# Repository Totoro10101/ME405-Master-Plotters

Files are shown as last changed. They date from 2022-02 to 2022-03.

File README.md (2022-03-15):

# ME405 Master Plotters
### A ME 405 term project that documents a pen plotter design.

The design we're going with is inspired by this YouTube video by DAZ projects: 

[the SIMPLEST cnc PEN PLOTTER | how to build it](https://www.youtube.com/watch?v=zFRRUZdz1HY)

Although we're taking inspriation from this design, we are making some changes that we believe will improve
its performance. The basic layout of this design is a 2.5-D pen plotter that is laid out horizontally on a flat base. The base is
is going to be a rectangular plywood piece with pulleys at each corner. There will be two gearmotors driving the pen plotter placed
at two adjacent corners (see sketch). The two motors will directly drive the two pulleys at the corners of the base, and the two other 
pulleys will be idlers which guide the belt. They will make the belt form one continuous loop in an hourglass shape.
Instead of using string like the video, we will use a GT2 timing belt to increase the traction on the pulley because of the teeth
present on the pulley wheels and the belts, and eliminate slipping. Since the total length of the belt will change slightly as the pen moves,
we will use a stretchy paracord joined with the timing belt to provide some room for movement while keeping tension. To actuate the pen and lift it
off of the paper when moving between drawn lines, we'll use a small servo that activates to lift the pen within its holder. This holder will have
ball rollers on the bottom to allow it to move smoothly over the paper.

A rough bill of materials is shown below. We're keeping the main motors simple and efficient by using the equipment available to us in lab. The GT2 belt and
pulleys will be purchased from Amazon and other components to hold the pen and servo and to mount the motors will be 3D printed by our group.

## Bill of Materials
| Qty. | Part | Source | Est. Cost |
|:----:|:---|:---|:---:|
|  2 | Pittperson Gearmotors | ME405 Tub | - |
|  1 | Nucleo with Shoe | ME405 Tub | - |
|  1 | GT2 Timing Belt | Amazon | $6.99 |
|  1 | GT2 Timing Pulleys | Amazon | $7.99 |
|  4 | Mini Ball Transfer Bearing | Amazon | $10.95  |
|  6 | Skateboard Bearings | Jackson | - |
|  1 | Sunfounder Micro Servo | Charlie | - | 
|  1 | Bungee Cord 1/8" Diameter | Amazon | $5.95 | 
|  1 | Small String | Tori | - |
|  2 | Limit Switches | Amazon | $2 |
|  1 | 3D print fillament | Jackson | - |

## Preliminary System Sketch
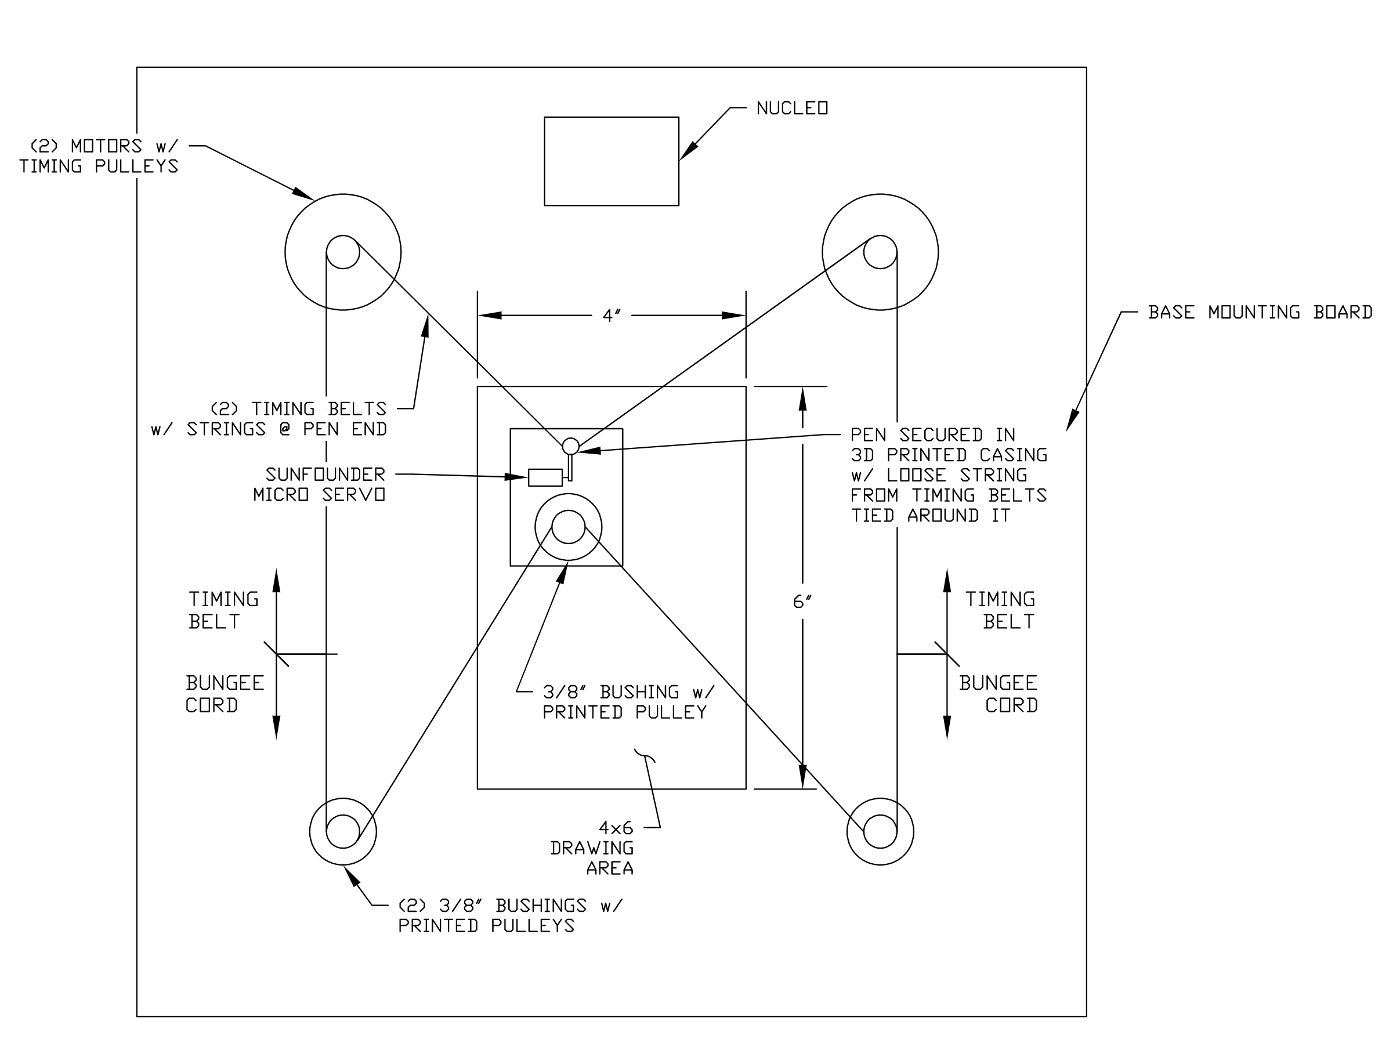
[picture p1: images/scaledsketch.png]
|  |
|:--:|
|**Figure 1: Scaled sketch showing the basic layout of our planned plotter**|

## Hardware Design
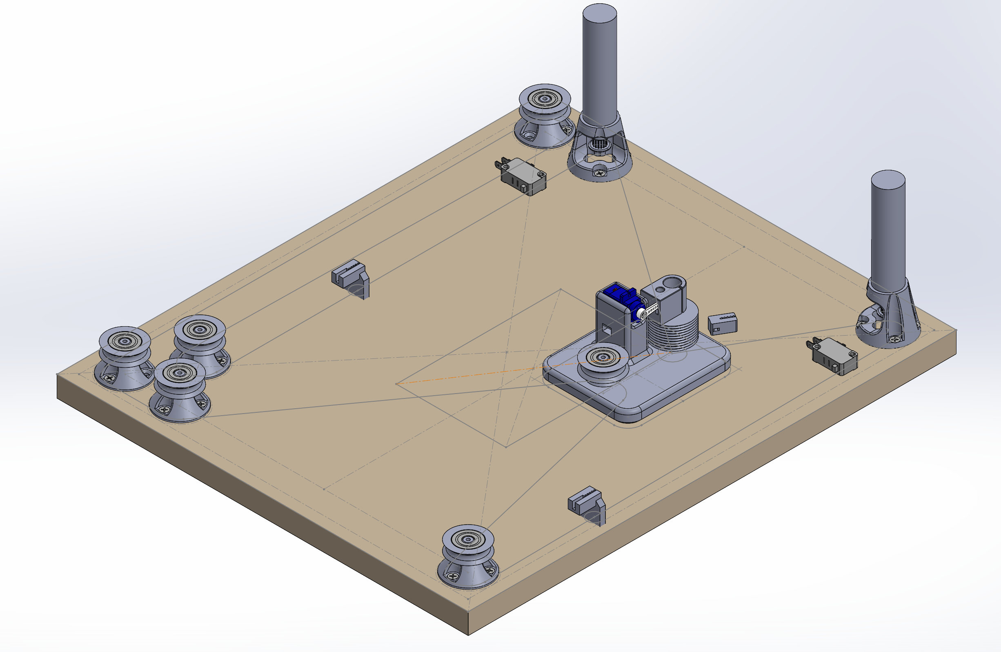
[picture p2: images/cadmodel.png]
|  |
|:--:|
|**Figure 2: CAD Model showing final version of Pen Plotter**|

The hardware we are using is mostly 3D printed from CAD designs created in Solidworks. The main components are the motor mounts, paracord pulleys, 
the pen carriage, and servo mount for actuating the pen. The motor mounts allow for mounting of our gearmotors vertically with the GT2 timing pulleys
housed within the mount and connected to the bungee cord. The pulleys at the adjacent corners that are not driven are using skateboard bearings mounted on top
of similar mounts to ensure the cord is at the same height as the timing belt. One feature that we added since the preliminary sketch phase was a wrap around
pulley for the bungee cord. The extra length of the cord wrapping around this additional pulley ensures we keep proper tension on the timing belt at all locations
in the drawing area, otherwise the bungee could loosen up too much and the belts would slip. The timing belt and cord are connected to the pen carriage at the top
and bottom of the rectangular carriage. There is a pulley on the back to allow the para cord to move smoothly, but the timing belts are attached using string to keep 
the distance constant from the gearmotors to the pen carriage. The pen is attached using a 3D printed holder that contains a cutout to press fit the sharpie into 
the hole. This is then connected to the servo that is mounted on the carriage using the small servo arm and an indentation for the servo to lift up the pen. The pen
carriage itself uses small ball transfer bearings to slide smoothly across the paper while the pen plots.

## Software Design
The software we designed uses a task based approach to update encoder positions and control set points based on a given HPGL file. The first process
to run is the start up process that zeros our encoders and puts the pen carriage in a known home position for us to use as a reference point to calculate 
set points from the HPGL file. The parsed HPGL file gives coordinates in the form of encoder ticks using a coordinate transformation that calculates it 
based on the HPGL and then sets the set point for each motor individually. The controller and encoder constantly update and share the data they collect
to tell whether the pen has reached the proper set point. 

For more detailed explanation on the tasks being performed, refer to our [Github Pages Documentation](https://totoro10101.github.io/ME405-Master-Plotters/)

## Results
The results of our pen plotter were very encouraging. By the end of thep project, we were able to perform relatively complex drawings that included both 
straight lines and curves, pen up and pen down commands, and could be taken from any file drawn in Inkscape so long as there were no memory issues with the
HPGL and the Nucleo. 

We tested the functionality of our pen plotter by providing it with multiple different HPGL files that we believed covered all the important aspects of the 
machine. We needed a file that would move in straight lines as well as curves and also required the lifting of the pen between operations. So long as the 
plotter was able to perform all of these tasks and draw the desired shapes, we believed it would be robust enough of a design to handle any HPGL file. 
The system performed fairly well in these tests once we got the controller set points and kinematics all correct. One minor issue is that the device moves 
more quickly in the direction that the bungee is pulling it in, so it was a little bit less accurate in that direction. Another thing we noticed in testing the 
plotting was that the Inkscape HPGL sometimes included a feature to run over all line commands twice, so it would draw something, and then attempt to go right back over it 
for a darker drawing. This functionality showed us that it wasn't perfectly repeatable due to some steady state error and overshoot in our controller or the bungee
affecting the path too much for repeatability, so the second time a line was plotted, it wasn't perfectly overlapping the original line. This could be fixed with 
some more tuning to controller gains or bungee length, but the variation in repeatability was small enough for our uses. 

## Future Work
Both the hardware and software of the plotter could be improved. One issue previously mentioned was the difference in speed when moving directions due to the
tension in the bungee being uneven for different positions of the pen. This could be mitigated by adding even more length to the bungee run, which makes the force more constant.
There was also some non-negligible friction in the bearings of the idler pulleys. If this were reduced, the difference in effort between each motor could be reduced.
Another way to reduce these effects could be to make the entire system larger, with longer belts, while retaining the same plotting area. The belts were able to stay on
their pulleys without slipping during operation, but this was marginal and they would slip if the pen ended up far outside the drawing area. This could potentially be reduced
with larger drive pulleys, though this would also increase the error from the true position that comes from our calculation of the kinematics of the system. We assume that the
belt extends from the center of the drive motor and its length is proportional to the angle which the pulley has rotated through, but neither of these is strictly true.
With a bigger pulley, we may need to revise this calculation to take into account the radius of the pulleys and the variable amount of belt that wraps around them
as the angle of the belt changes. This does have a unique solution for each point, but requires solving a system of equations since each belt affects the other.

Another improvement to the software would be the ability to draw images with a large number of points. However, we began to run into the limits of the Nucleo's
memory. This issue could be fixed in a few ways. First, it would be good to switch to reading the HPGL file sequentially instead of loading the entire contents into memory.
This alone would be an improvement, but to allow for any reasonable file to be drawn, it may be necessary to queue up points as the plotter is drawing. HPGL is read
sequentially, so it would be possible to integrate the parsing of the file into the multitasking loop, which would mean that the limitation would be the size of the flash
on the Nucleo. This is likely large enough for any reasonable plots, but if not external storage such as an SD card could be used, or HPGL could be sent over serial.

## Additional Links
[Github Pages Documentation](https://totoro10101.github.io/ME405-Master-Plotters/)

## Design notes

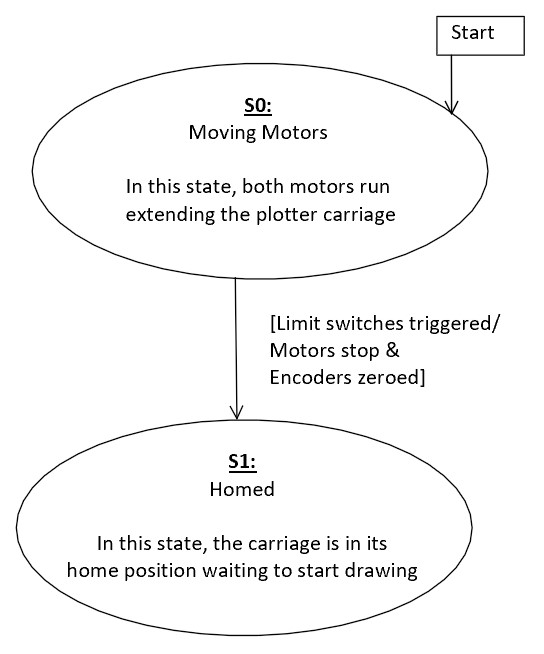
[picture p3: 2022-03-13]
docs/task_startup_FSM.jpg

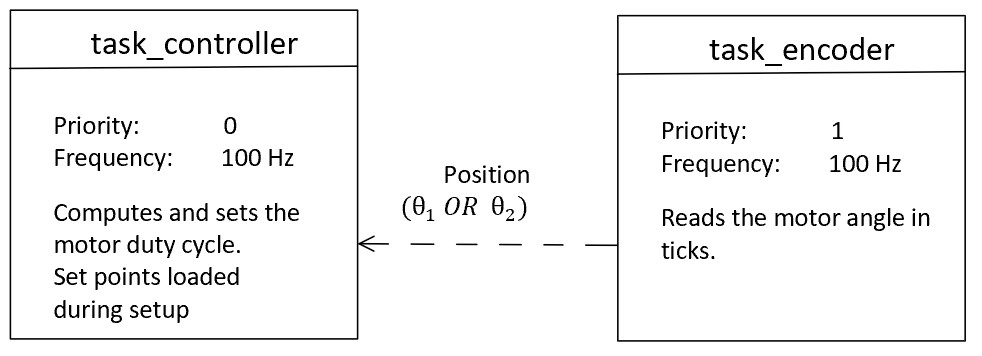
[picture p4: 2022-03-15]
docs/task_diagram.jpg

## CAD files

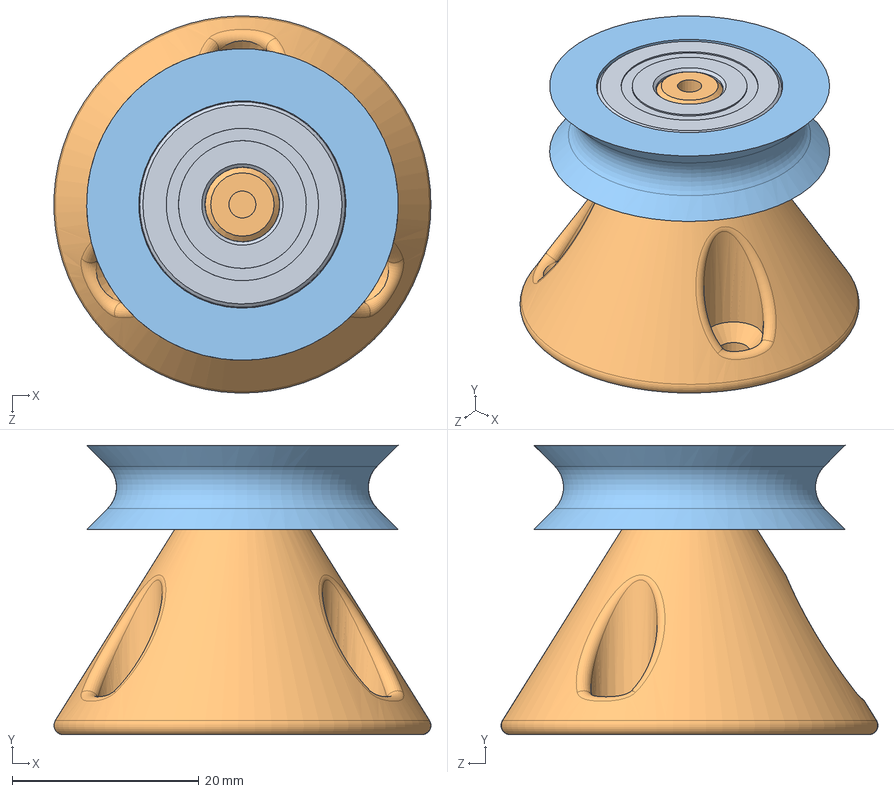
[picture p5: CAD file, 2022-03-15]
cad/solidworks/idler mounted.SLDASM
40.4 x 31.0 x 40.4 mm
6661K12_Ball Bearing
idler mount
idler pulley

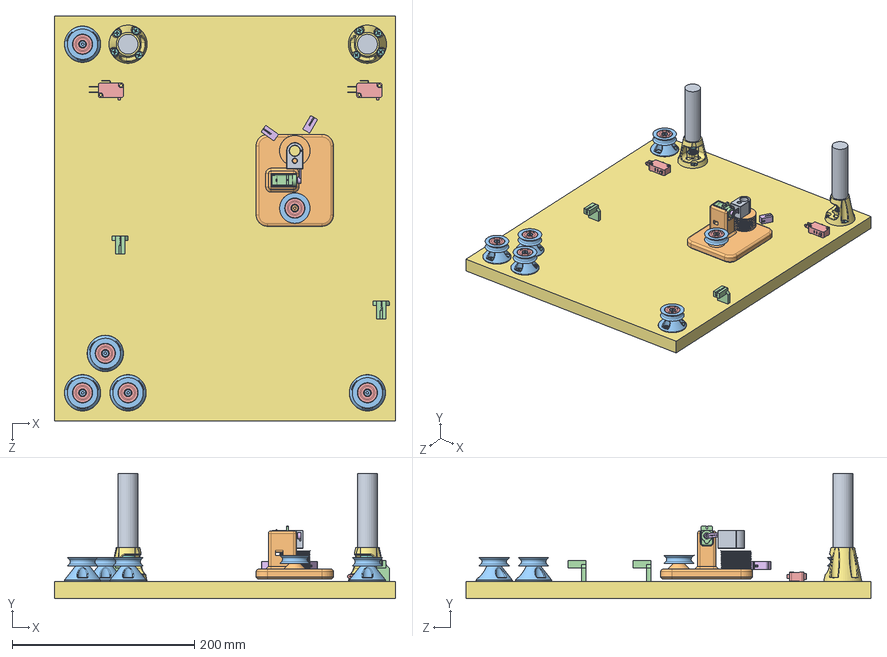
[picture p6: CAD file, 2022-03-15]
cad/solidworks/plotter.SLDASM
375.0 x 137.5 x 445.0 mm
pen holder
carriage
idler pulley x 6
SG90 - Micro Servo 9g - Tower Pro.1
6661K12_Ball Bearing x 6
SG90 - Micro Servo 9g - Tower Pro.2
motor mount x 2
16t 6mm gt2 pulley 6mm bore x 2
pittmann motor x 2
91290A111_Black-Oxide Alloy Steel Socket Head Screw x 8
idler mount x 5
big tab clip x 2
7779K41_Miniature Snap-Acting Switch x 2
belt clip tie x 2
Part2^plotter
90031A151_Phillips Flat Head Screws for Wood x 21

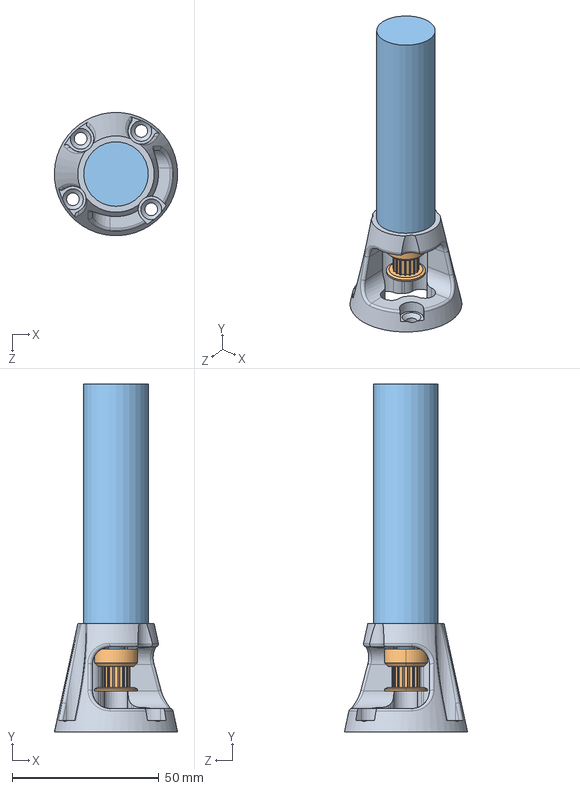
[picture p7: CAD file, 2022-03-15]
cad/solidworks/motor mounted.SLDASM
42.0 x 118.5 x 42.0 mm
motor mount
16t 6mm gt2 pulley 6mm bore
pittmann motor
91290A111_Black-Oxide Alloy Steel Socket Head Screw x 4

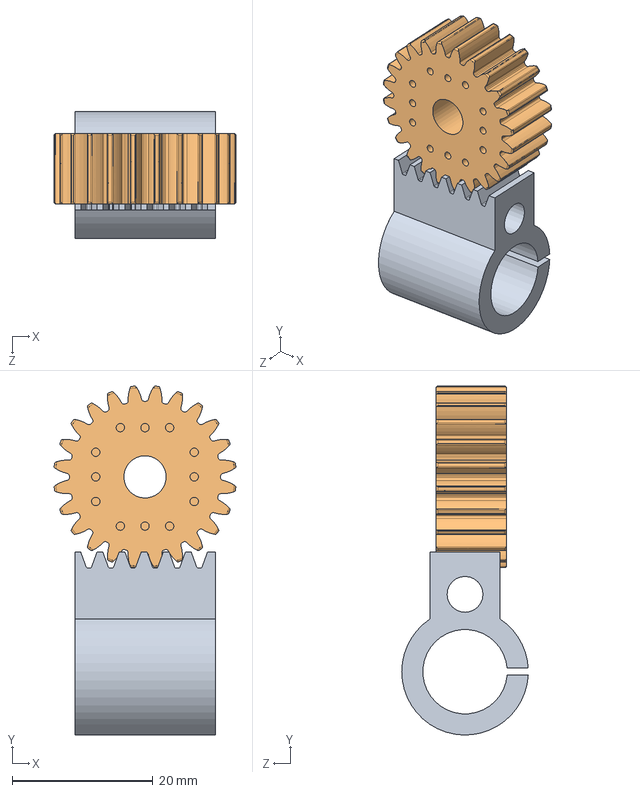
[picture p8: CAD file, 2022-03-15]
cad/solidworks/pen mount.SLDASM
25.8 x 49.6 x 18.0 mm
pen holder
2664N542_Metal Gear - 20 Degree Pressure Angle

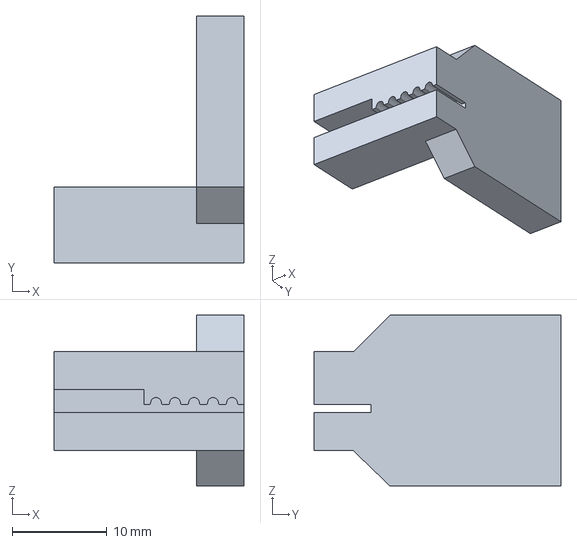
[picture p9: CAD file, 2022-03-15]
cad/3mf/belt clip tab.3MF
20.0 x 26.0 x 18.0 mm

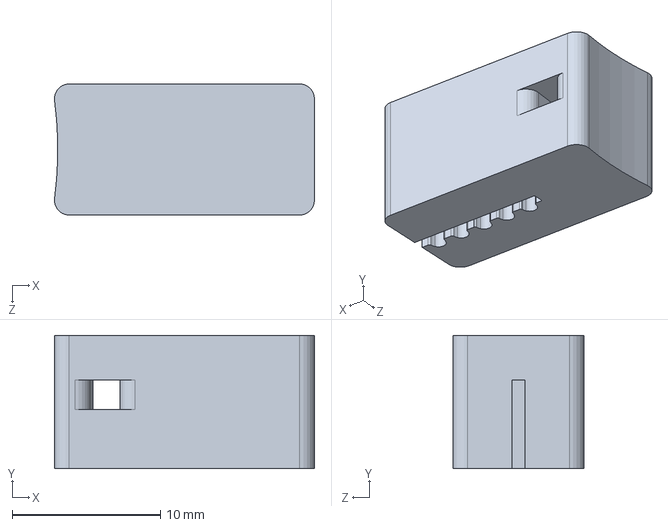
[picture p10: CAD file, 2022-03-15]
cad/solidworks/belt clip tie.SLDPRT
17.5 x 9.00 x 8.85 mm

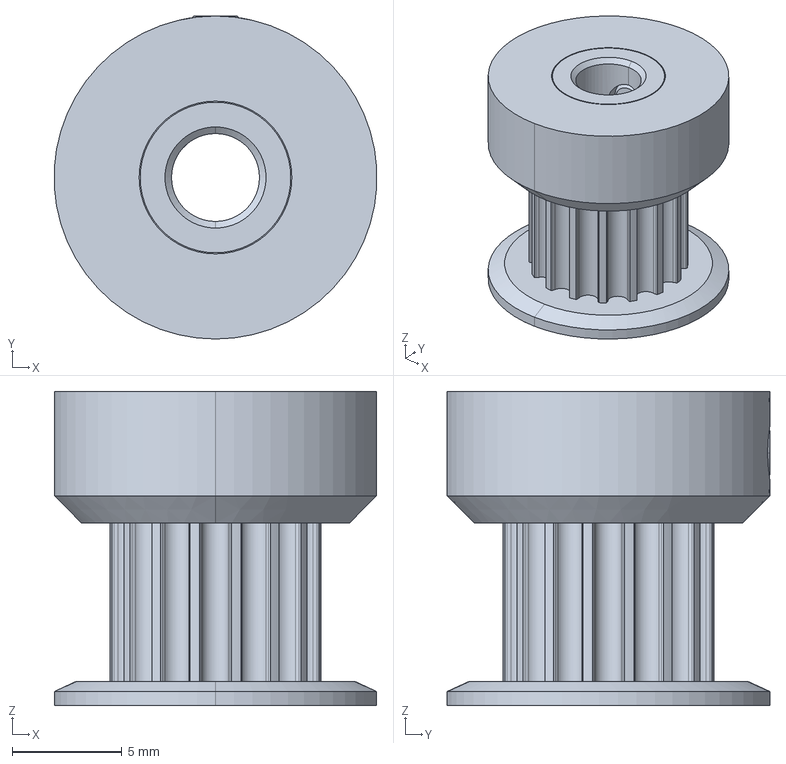
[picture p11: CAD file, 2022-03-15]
cad/solidworks/SDP_sdpsi_a_6a51m016df0604.stp
14.7 x 14.7 x 14.3 mm

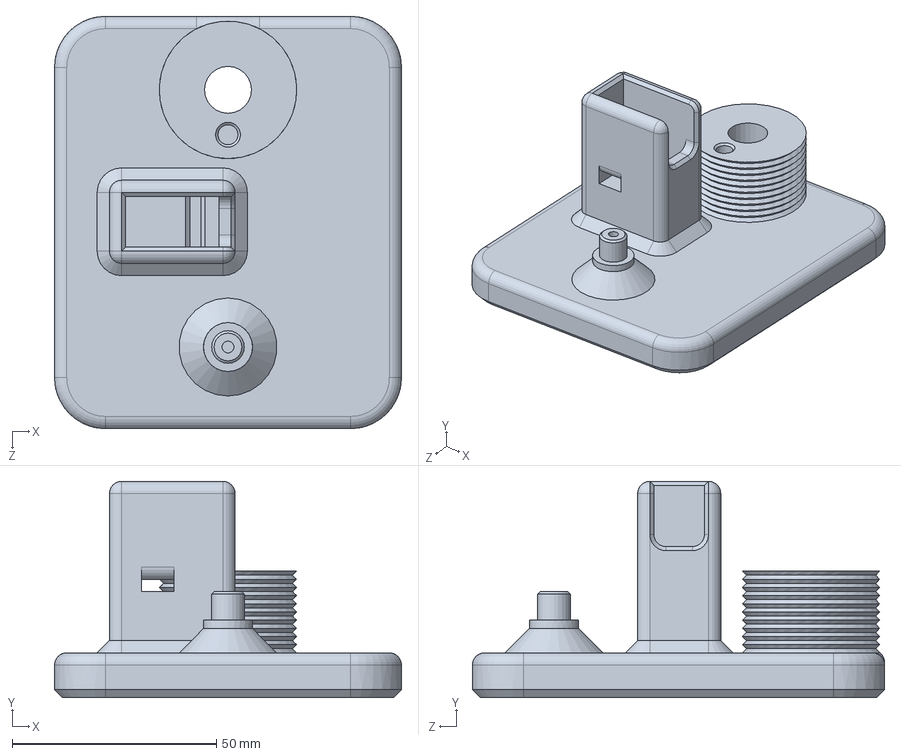
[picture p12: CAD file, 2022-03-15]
cad/solidworks/carriage.SLDPRT
85.0 x 53.0 x 101.0 mm

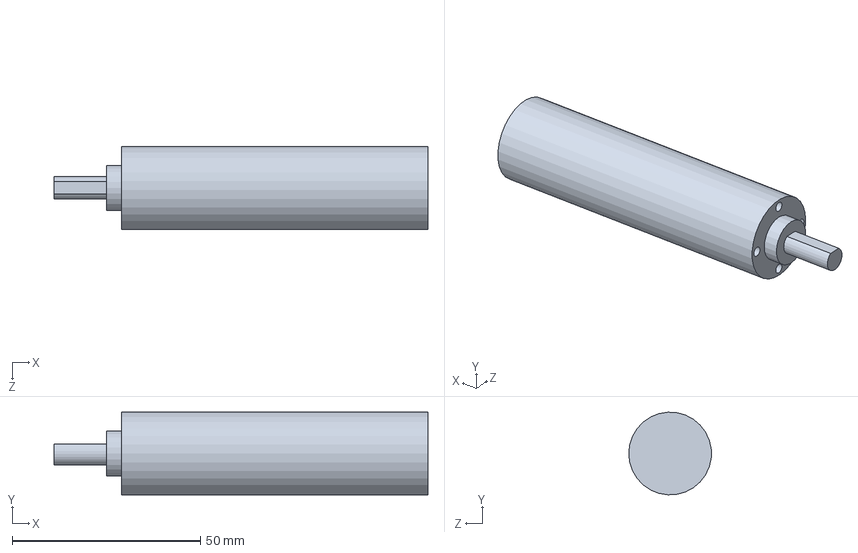
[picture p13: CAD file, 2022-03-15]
cad/solidworks/pittmann motor.SLDPRT
99.4 x 22.0 x 21.9 mm

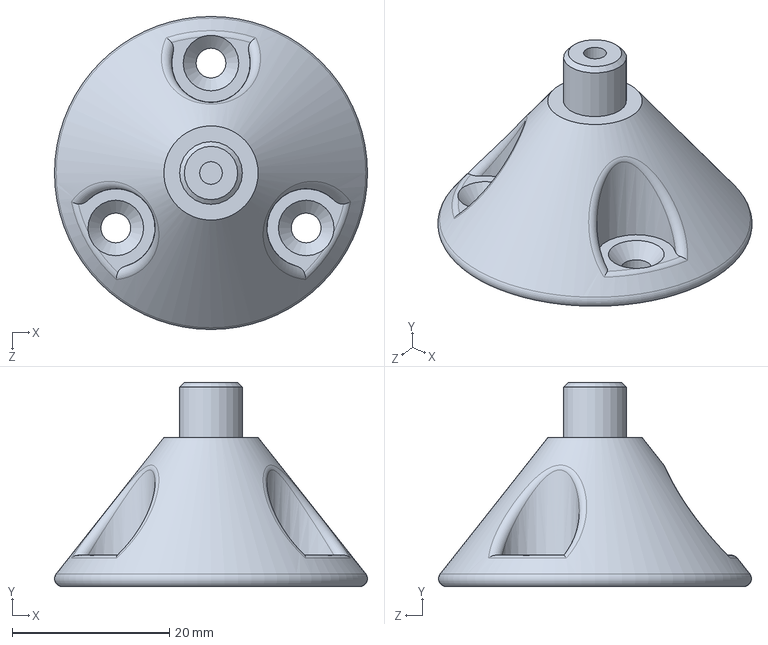
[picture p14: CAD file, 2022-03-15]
cad/solidworks/idler mount.SLDPRT
39.9 x 26.0 x 39.9 mm

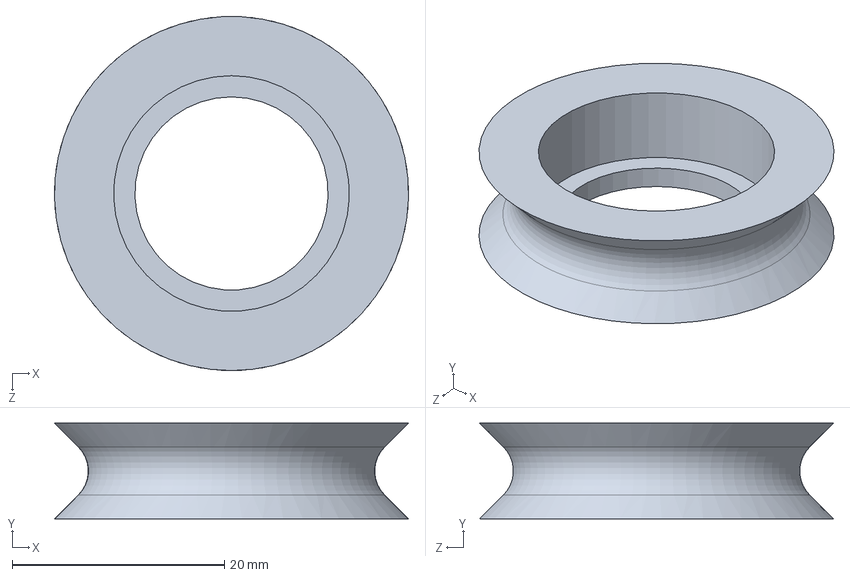
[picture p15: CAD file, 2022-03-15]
cad/solidworks/idler pulley.SLDPRT
33.3 x 9.00 x 33.4 mm

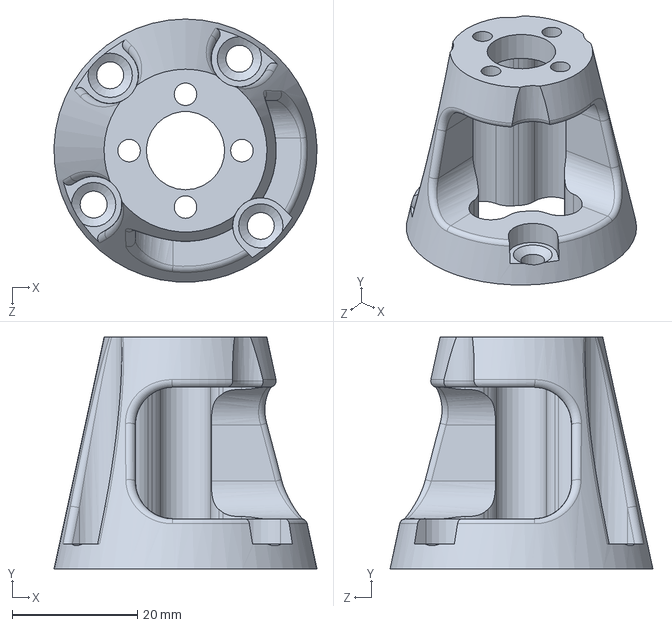
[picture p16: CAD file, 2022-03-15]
cad/solidworks/motor mount.SLDPRT
42.0 x 37.0 x 42.0 mm

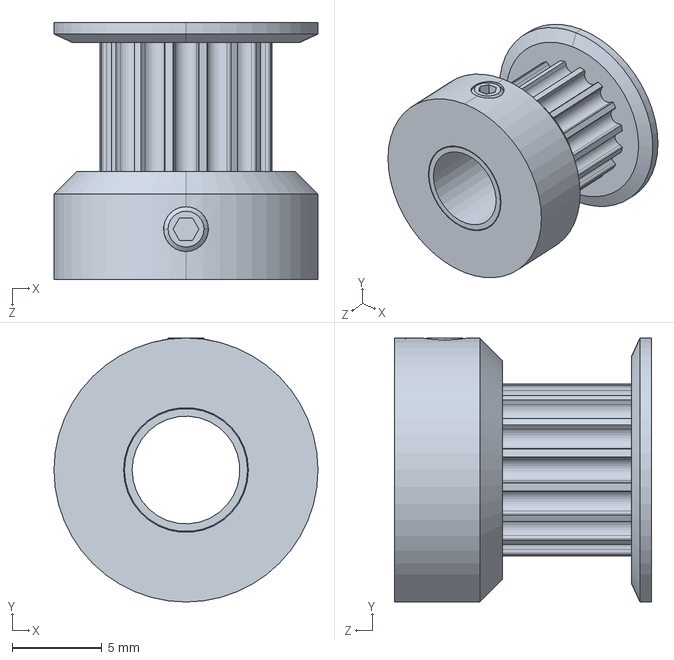
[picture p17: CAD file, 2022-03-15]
cad/solidworks/16t 6mm gt2 pulley 6mm bore.SLDPRT
14.7 x 14.7 x 14.3 mm

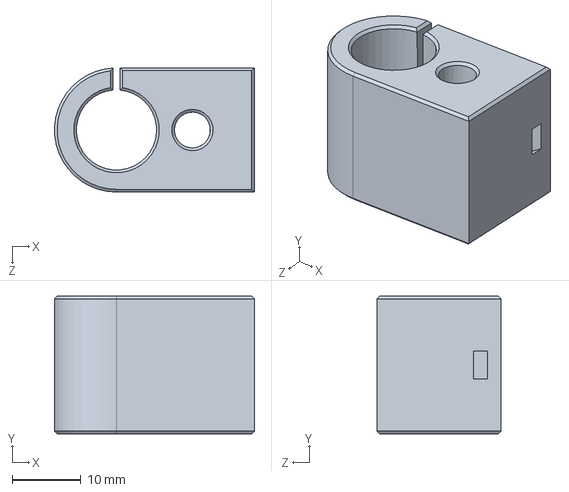
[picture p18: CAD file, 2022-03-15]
cad/solidworks/pen holder.SLDPRT
29.0 x 20.0 x 18.0 mm

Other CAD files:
cad/solidworks/big tab clip.SLDPRT
cad/solidworks/SG90 - Micro Servo 9g - Tower Pro.1.SLDPRT
cad/solidworks/SG90 - Micro Servo 9g - Tower Pro.2.SLDPRT
cad/solidworks/90031A151_Phillips Flat Head Screws for Wood.SLDPRT
cad/3mf/belt clip tie.3MF
cad/3mf/carriage.3MF
cad/3mf/idler mount.3MF
cad/3mf/idler pulley.3MF
cad/3mf/motor mount.3MF
cad/solidworks/2664N542_Metal Gear - 20 Degree Pressure Angle.SLDPRT
cad/solidworks/6661K12_Ball Bearing.SLDPRT
cad/solidworks/7779K41_Miniature Snap-Acting Switch.SLDPRT
cad/solidworks/91290A111_Black-Oxide Alloy Steel Socket Head Screw.SLDPRT
cad/stl/belt clip tab.STL
cad/stl/belt clip tie.STL
cad/stl/carriage.STL
cad/stl/idler mount.STL
cad/stl/idler pulley.STL
cad/stl/motor mount.STL

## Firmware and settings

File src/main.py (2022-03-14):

"""!
@file main.py
    This file contains a program that operates a 2.5 dimensional pen
    plotter using a task based approach. 

@author             Tori Bornino
@author             Jackson McLaughlin
@author             Zach Stednitz
@date               March 15, 2022

@date   2021-Dec-15 JRR Created from the remains of previous example
@copyright (c) 2015-2021 by JR Ridgely and released under the GNU
    Public License, Version 2. 
"""
import pyb
import time
import gc

import task_share
import cotask

import encoder
import motor
import servo
import controller
import task_parser

## @brief   Encoder pulses (ticks) per revolution
#  @details The encoder pulses or ticks per revolution of the pulley is 256
#           counts per revolution times 4 pulses per count for a quadrature
#           encoder time 16 for the 16:1 ratio between the backshaft of the
#           motor where the encoder is and the output shaft of the gearbox
#           where the pulley is.
PPR = 256*4*16

# Gains for motor PID controller (using P only)
_KP = 4*(360/PPR)
_KI = 0*(360/PPR)
_KD = 0*(360/PPR)

## @brief Encoder ticks per mm of belt length change.
#  @details There are 512 ticks/mm because there are 16 teeth on the drive
#           pulleys, at 2mm pitch, for 32mm of belt length per revolution.
#           Dividing the _PPR of the encoder by 32mm gives 512 ticks/mm. 
TICKS_PER_MM = 512
## @brief Maximum length of either belt.
R_MAX = 330 # mm
## @brief Maximum position of either motor (ticks).
TICKS_MAX = TICKS_PER_MM * R_MAX

# Motor IDs
_MOTOR1 = 0
_MOTOR2 = 1

##  @brief The servo pwm to set when the pen is up (% duty cycle)
UP = 8
##  @brief The servo pwm to set when the pen is down (% duty cycle)
DOWN = 7

def startup():
    '''!
    This method will initialize the pen plotter.
    
    This process includes running the motors until the limit switches are
    triggered. The pen will be up during this routine.
    '''
    servo1.set_angle(UP)
    zeroed1 = False
    zeroed2 = False
    print('starting up...')
    motor1.set_duty_cycle(-70)
    motor2.set_duty_cycle(70)
    while not zeroed1 or not zeroed2:
        if limit1_pin.value() == 0 and not zeroed1:
            print('Motor 1 zeroed')
            motor1.set_duty_cycle(0)
            zeroed1 = True
        if limit2_pin.value() == 0 and not zeroed2:
            print('Motor 2 zeroed')
            motor2.set_duty_cycle(0)
            zeroed2 = True
    print('startup finished')
    
def task_enc1_fun():
    """!
    Task which reads encoder 1 position
    """
    while True:
        value = encoder1.read()
        encoder1_share.put(value)
        yield ()

def task_enc2_fun():
    """!
    Task which reads encoder 2 position
    """
    while True:
        value = encoder2.read()
        encoder2_share.put(value)
        yield ()
        
def task_controller_fun ():
    """!
    Task that runs a PID controller that controls both motors and the servo.
    """
    # States of controller FSM
    STATE_MOTOR = 0
    STATE_SERVO = 1
    
    # Set the position of the encoders to the zeroing position. This must be
    # done after encoder tasks run the first time to clear accumulated ticks
    # from the zeroing process.
    encoder1.set_position(TICKS_MAX)
    encoder2.set_position(TICKS_MAX)
    
    # Initial state: Motor is controlled and pen is up from startup
    state = STATE_MOTOR
    curr_servo_state = 0
    servo_start_time = None
    
    # Load the first setpoint
    if sp_theta1_queue.any():
        next_th1_sp = sp_theta1_queue.get()
        next_th2_sp = sp_theta2_queue.get()
        next_pen_sp = sp_pen_queue.get()
    pidController.set_set_point((next_th1_sp, next_th2_sp))
    
    
    while True:
        # Always update the controller first
        motor1.set_duty_cycle(pidController.run(_MOTOR1))
        motor2.set_duty_cycle(pidController.run(_MOTOR2))
        
        if state == STATE_MOTOR:
            move_done = pidController.check_finish_step()
            if move_done:
                # Retrieve the next setpoint in the queue, but don't update
                # the controller yet (pen may need to move)
                if sp_theta1_queue.any():
                    next_pen_sp = sp_pen_queue.get()
                    next_th1_sp = sp_theta1_queue.get()
                    next_th2_sp = sp_theta2_queue.get()
                if next_pen_sp == curr_servo_state:
                    # Update controller if pen is already in position
                    pidController.set_set_point((next_th1_sp, next_th2_sp))
                else:
                    # If pen position needs to change, go to servo state
                    state = STATE_SERVO
            
        elif state == STATE_SERVO:
            # Time that the servo needs to change position
            SERVO_WAIT = 500 # ms
            if servo_start_time == None:
                servo_start_time = time.ticks_ms()
                if curr_servo_state == 0:
                    servo1.set_angle(DOWN)
                elif curr_servo_state == 1:
                    servo1.set_angle(UP)
            # Wait for servo
            elif time.ticks_diff(time.ticks_ms(),
                                 servo_start_time) > SERVO_WAIT:
                pidController.set_set_point((next_th1_sp, next_th2_sp))
                curr_servo_state = next_pen_sp
                servo_start_time = None
                state = STATE_MOTOR
        yield ()
        
if __name__ == "__main__":
    # Create 2 limit switch shares to share limit switch condition.
    # 1 is unpressed, 0 is pressed (active-low configuration).
    limit1_share = task_share.Share('i', thread_protect=False,
                                    name="Limit 1 Share")
    limit2_share = task_share.Share('i', thread_protect = False,
                                    name = "Limit 2 Share")
    
    # Create 2 encoder shares to share position data.
    encoder1_share = task_share.Share('i', thread_protect = False,
                                      name = "Encoder 1 Share")
    encoder2_share = task_share.Share('i', thread_protect = False,
                                      name = "Encoder 2 Share")

    # Create Queues with set points (theta_1, theta_2, Pen_up/down) (ticks).
    sp_theta1_queue = task_share.Queue('i', 2000)
    sp_theta2_queue = task_share.Queue('i', 2000)
    sp_pen_queue = task_share.Queue('i', 2000)
    
    # Create the HPGL parser.
    parser = task_parser.Parser(sp_theta1_queue, sp_theta2_queue, sp_pen_queue)
    
    # Instantiate encoders with default pins and timer.
    encoder1 = encoder.EncoderDriver(pyb.Pin.cpu.B6, pyb.Pin.cpu.B7, 4)
    encoder2 = encoder.EncoderDriver(pyb.Pin.cpu.C6, pyb.Pin.cpu.C7, 8)
    
    # Instantiate limit switches
    limit2_pin = pyb.Pin(pyb.Pin.cpu.C2, pyb.Pin.IN)
    limit1_pin = pyb.Pin(pyb.Pin.cpu.C3, pyb.Pin.IN)
    
    # Instantiate servo
    servo1 = servo.Servo(pin1 = pyb.Pin.board.PA9,
                         timer = pyb.Timer(1, freq=50), channel = 2)
    
    # Instantiate motors with default pins and timer
    motor1 = motor.MotorDriver(pyb.Pin.board.PC1, pyb.Pin.board.PA0,
                               pyb.Pin.board.PA1, pyb.Timer(5, freq=20000))
    motor2 = motor.MotorDriver(pyb.Pin.board.PA10, pyb.Pin.board.PB4,
                            pyb.Pin.board.PB5, pyb.Timer(3, freq=20000))
    
    # Instantiate proportional controller with initial gains and setpoint
    pidController = controller.PIDController(1, 0, 0, (TICKS_MAX, TICKS_MAX),
                                             encoder1_share, encoder2_share)
    pidController.set_gains(_KP, _KI, _KD)

    # Create the tasks. If trace is enabled for any task, memory will be
    # allocated for state transition tracing, and the application will run out
    # of memory after a while and quit. Therefore, use tracing only for 
    # debugging and set trace to False when it's not needed.
    task_encoder1 = cotask.Task(task_enc1_fun, name='Encoder_1_Task',
        priority=3, period=10, profile=True, trace=False)
    task_encoder2 = cotask.Task(task_enc2_fun, name = 'Encoder_2_Task',
        priority=3, period=10, profile=True, trace=False)
    task_controller = cotask.Task(task_controller_fun, name='Controller_Task',
        priority=1, period=10, profile=True, trace=False)
    
    cotask.task_list.append(task_encoder1)
    cotask.task_list.append(task_encoder2)
    cotask.task_list.append(task_controller)

    # Run the memory garbage collector to ensure memory is as defragmented as
    # possible before the real-time scheduler is started
    gc.collect()

    # Run the startup routine to home the encoders 
    startup()
    # parse the selected HPGL file
    parser.read('WE_ARE_AWESOME.hpgl')
    
    # Run the scheduler with the chosen scheduling algorithm.
    # Quit if KeyboardInterrupt.
    while True:
        try:
            cotask.task_list.pri_sched()
        except KeyboardInterrupt:
            motor1.set_duty_cycle(0)
            motor2.set_duty_cycle(0)
            print('disabled')
            break

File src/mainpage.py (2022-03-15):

'''!@file       mainpage.py
    Main page for ME 405 Term Project: Master Plotters

    @mainpage

    @section sec_intro  Introduction
                        This is the documentation site for Tori Bornino,
                        Jackson Mclaughlin, and Zachary Stednitz's code used in
                        ME 405 - Mechatronics, Term Project: It's a Plot  
                        Implementation, taught in Winter 2022 by Dr. John 
                        Ridgely. Source code is available at:
                        https://github.com/Totoro10101/ME405-Master-Plotters
    
    @section sec_sch    Software Design
                        Before the pen plotter draws the given image, the plotter
                        is zeroed and the given HPGL is parsed.
                        
                        During general operation the pen plotter has two main tasks:
                        encoder and controller. The encoders running consecutively read 
                        the motor positions and the controller uses the positions to
                        controll the motors. The desired plotter position is loaded
                        during startup. 
                        @image html task_diagram.jpg width=40% \n
                            
    @subsection subsec_sch1 Startup
                            Before the pen plotter plots the drawing, it will zero its position. 
                            Zeroing the encoder is important to ensuring we start plotting the
                            given image at a known location. It utilizes two limit switches to 
                            determine the carriage zero point where the plotter carriage is
                            completely extended. 
                            
                            @image html task_startup_FSM.jpg width=25% \n
                            
    @subsection subsec_sch2 task_parser
                            Parses the HPGL file for a given image outputting the required pen locations in ticks and
                            pen states to construct the drawing. These include "pen advance" and lifting the pen
                            off of the paper when not plotting. Parser task doesn't require a finite state machine
                            since it's only purpose is to read the HPGL data and doesn't transition to any other state.
                            However, the kinematic equations used in the derivation of the transition are further
                            explained in the @ref page_kinetics page.
                            
    @subsection subsec_sch3 task_encoder
                            Reads the position of the encoder on each motor and stores them in a share.
                            This task does not require a finite state machine since it is only reading
                            the position of the motor and the zeroing takes place in the startup task.
                            
    @subsection subsec_sch4 task_controller
                            Controls the motor duty cycle and servo position based on set points stored in the  
                            set point queues. The controller task has two states: Motor and Servo. When a new set
                            point is loaded, the pen condition is checked, and corrected, before transitioning
                            back to the motor state until the next desired position is reached. The controller
                            driver uses PID closed loop control to set the motor duty cycle and move the pen
                            to the desired location. 
                            
                            @image html task_controller_FSM.jpg width=30% \n
                            
    
                            
    @author             Tori Bornino
    @author             Jackson McLaughlin
    @author             Zach Stednitz
    @date               March 15, 2022
'''

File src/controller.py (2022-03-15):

'''!@file controller.py
    A class that performs closed loop PID control.
    
    @author     Tori Bornino
    @author     Jackson McLaughlin
    @author     Zach Stednitz
    @date       March 15, 2022
'''

import time

# Motor IDs
_MOTOR1 = 0
_MOTOR2 = 1

## @brief Maximum allowable power to set on the motors (percent duty cycle).
MAX_POWER = 100

class PIDController:
    '''! 
    This class implements a PID controller to run a pen plotter.
    It contains methods for calculating the actuation value 
    and setting the Kp, Ki, and Kd gains. 
    ''' 
    
    def __init__ (self, Kp, Ki, Kd, set_point, sensor_share1, sensor_share2):
        '''! 
        Creates a PID controller by initializing controller gains and storing
        the queue of setpoints and (2) shares with sensor data. 
        
        @param Kp               The proportional gain for the controller.
                                Units of (dutyCycle/ticks)
        @param Ki               The integral gain for the controller.
                                Units of (dutyCycle/(ticks*seconds))
        @param Kd               The derivative gain for the controller.
                                Units of (dutyCycle/(ticks/seconds))
        @param set_point        The initial setpoint value.  
        @param sensor_share1    A share that contains the read position from
                                sensor 1 in a (2) sensor system with
                                independently controlled actuators.
        @param sensor_share2    A share that contains the read position from
                                sensor 2 in a (2) sensor system with
                                independently controlled actuators.
        '''
        self._set_point = set_point
        self._Kp = Kp
        self._Ki = Ki
        self._Kd = Kd
        self._sensor_share = [sensor_share1, sensor_share2]

        # Step response start time for each motor
        self._step_start_time = [None, None]

        # Store data to calculate actuation values
        self._error = [0, 0]
        self._last_time = [0, 0]
        self._last_error = [0, 0]
        self._Iduty = [0, 0]

    def run(self, motorID):
        '''! 
        Runs the control algorithm. Reads the position data from a
        sensor and then finds the error between the actual position and the 
        desired set point value. Then calculates the setpoint value.
        
        @param  motorID The motor that you are controlling.
        @return The actuation value to fix steady state error. When in the servo
                state, the actuation value is the servo pwm. If the actuation
                value is True, then the state changes to motor. When in the
                motor state, then actuation value is a tuple for motors (1, 2)
                of the duty cycle. If the actuation value is False,
                then the state changes to servo.
        '''
        # Store initial motor step time
        if self._step_start_time[motorID] == None:
            self._step_start_time[motorID] = time.ticks_ms()
            self._last_time[motorID] = self._step_start_time[motorID]
        
        # Calculate the current error in position
        self._error[motorID] = self._sensor_share[motorID].get() - self._set_point[motorID]
        curr_time = time.ticks_diff(time.ticks_ms(),self._step_start_time[motorID])
        
        # Calculate the PID actuation value
        # Proportional component of actuation value
        Pduty = -self._Kp*self._error[motorID]
        
        # Integral component of actuation value
        _Iduty_new = self._Ki*self._error[motorID]*(curr_time - self._last_time[motorID])
        if (self._Iduty[motorID] > 0 and _Iduty_new < 0) \
            or  (self._Iduty[motorID] < 0 and _Iduty_new > 0):
            self._Iduty[motorID] = _Iduty_new
        else:
            self._Iduty[motorID] += _Iduty_new
        
        # Differential component of actuation value
        Dduty = self._Kd*(self._error[motorID]-self._last_error[motorID])/(curr_time - self._last_time[motorID])
        
        # Total PID actuation value
        actuation_value = Pduty + self._Iduty[motorID] + Dduty

        # Filter saturated values
        if actuation_value > MAX_POWER:
            actuation_value = MAX_POWER
        elif actuation_value < -MAX_POWER:
            actuation_value = -MAX_POWER

        # Store values for next iteration
        self._last_error[motorID] = self._error[motorID]
        self._last_time[motorID] = curr_time

        # Compensate for swapped directions on each motor due to belt
        if motorID == _MOTOR1:
            return -actuation_value
        elif motorID == _MOTOR2:
            return actuation_value

    def set_gains(self, Kp, Ki, Kd):
        '''! 
        Sets the proportional gain controller value.
        
        @param Kp           The proportional gain for the controller.
                            Units of (dutyCycle/ticks)
        @param Ki           The integral gain for the controller.
                            Units of (dutyCycle/(ticks*seconds))
        @param Kd           The derivative gain for the controller.
                            Units of (dutyCycle/(ticks/seconds))
        '''
        self._Kp = Kp
        self._Ki = Ki
        self._Kd = Kd
        
    def set_set_point(self, set_point):
        '''! 
        Sets the desired setpoint for the step response.
        
        @param set_point  The desired steady state response value. It is in the
                          form of a tuple (theta_1, theta_2, pen) in ticks.
        '''
        self._set_point = set_point
        
        # Step response start time for each motor
        self._step_start_time = [None, None]
        
        # Store data to calculate actuation values
        self._error = [0, 0]
        self._last_time = [0, 0]
        self._last_error = [0, 0]
        self._Iduty = [0, 0]
        
    def check_finish_step(self):
        '''!
        Check if current set point has been reached by both motors.
        
        @return a boolean is returned for if the setpoint has been reached.
        '''
        done = False
#         print(self._error[_MOTOR1], self._error[_MOTOR2])
        if abs(self._error[_MOTOR1]) < 1000 and abs(self._error[_MOTOR2]) < 1000:
            self._step_start_time = [None, None]
            self._error = [0, 0]
            done = True
        return done

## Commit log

2022-03-03 updated task controller to accommodate two motors
2022-03-05 Update controller
    Have the controller compute the duty cycles for each motor at the same time
2022-03-06 Add servos
    Add servos and add tests for servos and motors
2022-03-06 Add startup
    include startup function in main, move state change from motor to servo to main from controller and add set_position to encoder
2022-03-07 attempt 1 at adding limit switches to startup
2022-03-07 last class stuff (limit switches not working)
    [encoder.py, main.py, test_parser.py]
2022-03-09 fixed servo, need to fix motor/servo timing
    [main.py, test_parser.py]
2022-03-13 servo cleanup
2022-03-13 Update servo.py
    Finalize the doxygen for servo
2022-03-15 add cad
    [16t 6mm gt2 pulley 6mm bore.SLDPRT, 2664N542_Metal Gear - 20 Degree Pressure Angle.SLDPRT, 6661K12_Ball Bearing.SLDPRT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]
2022-03-15 kinematics page
    kinematics page
